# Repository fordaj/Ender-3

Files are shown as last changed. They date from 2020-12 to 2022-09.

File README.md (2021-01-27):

# Ender-3
I run a small print farm for my business, fordworks3D, LLC. It is currently made up of 4 Ender 3 Pros, and this is where you can find my project upgrades, Octoprint network setup, Marlin configurations, and more.

<p align="center">
    <a href="https://www.etsy.com/shop/fordworks3D">fordworks3D Logo</a>
</p>
<p align="center">
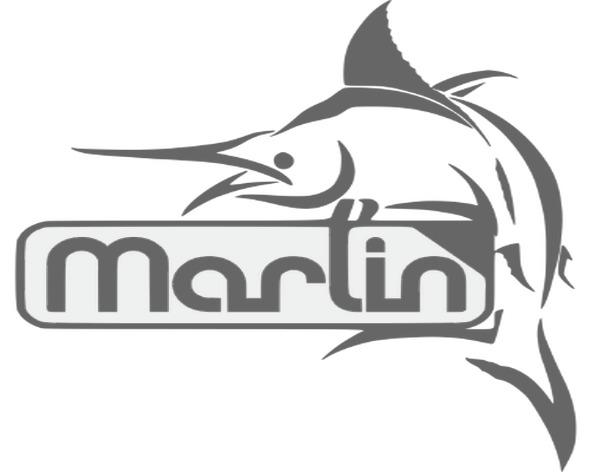
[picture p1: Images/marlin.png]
Marlin Logo
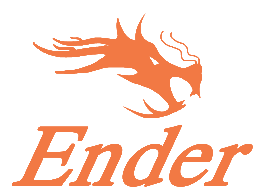
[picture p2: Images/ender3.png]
Ender 3 Logo
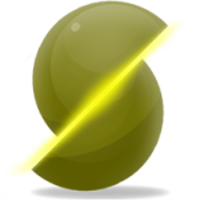
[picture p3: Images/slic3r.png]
Slic3r Logo
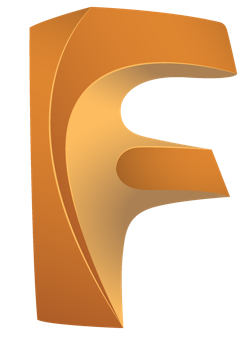
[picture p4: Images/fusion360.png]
Fusion 360 Logo
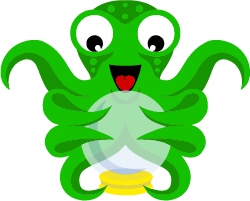
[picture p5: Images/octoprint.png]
Octoprint Logo
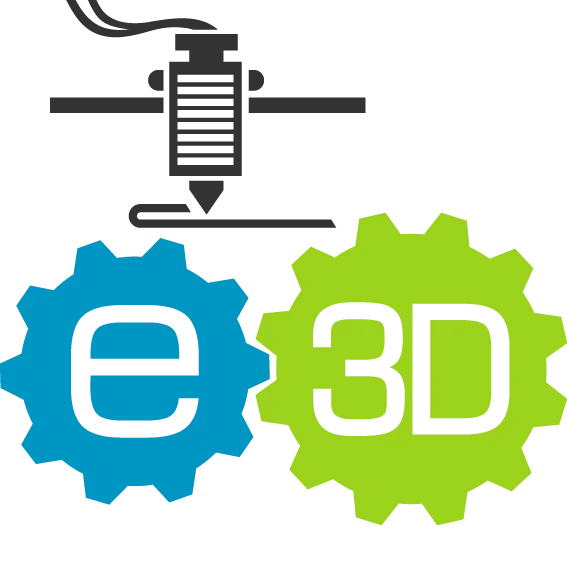
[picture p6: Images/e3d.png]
E3D Logo
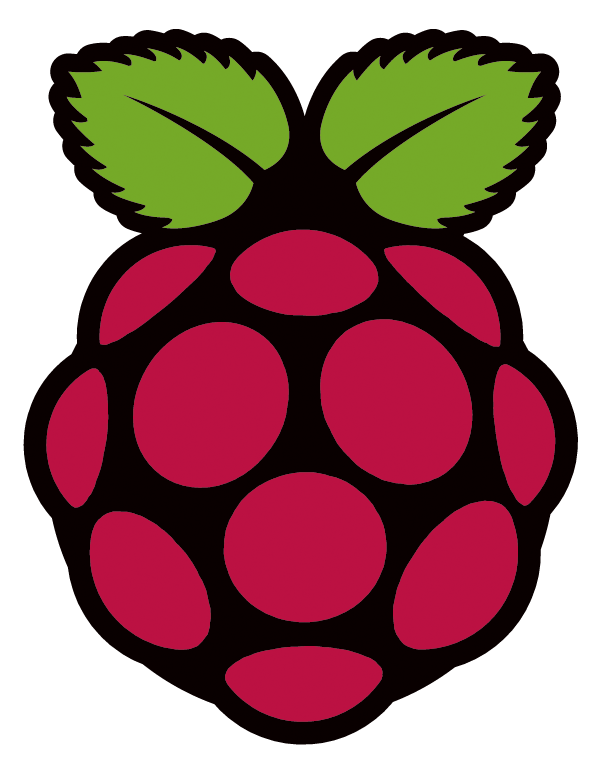
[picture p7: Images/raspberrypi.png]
Raspberry Pi Logo
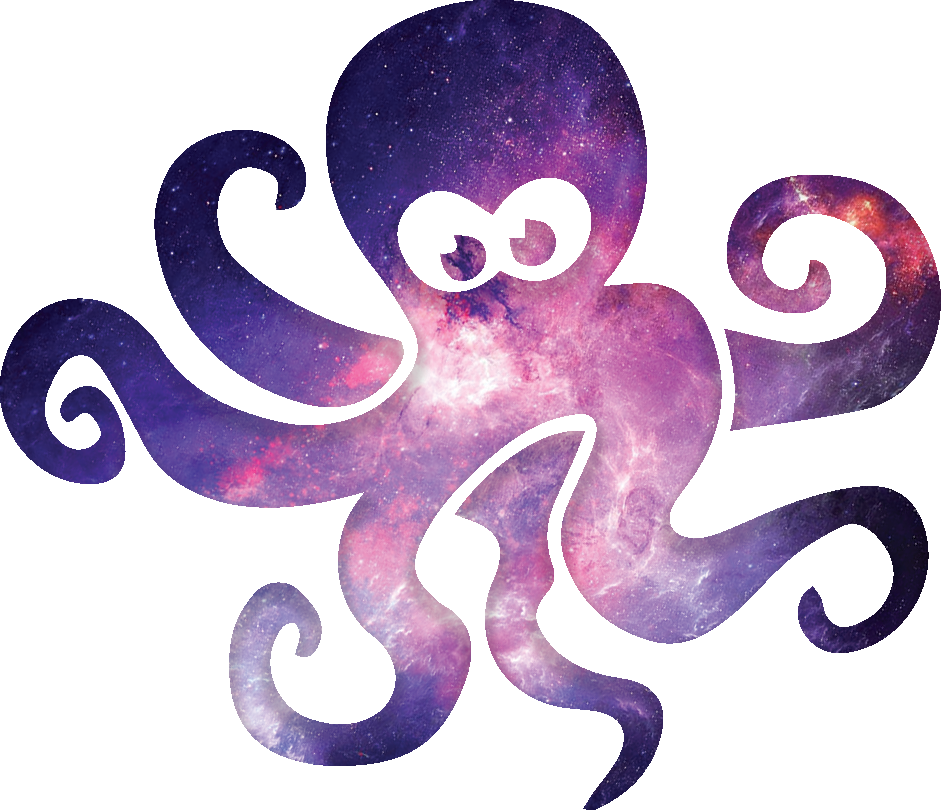
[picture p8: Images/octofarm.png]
Octofarm Logo
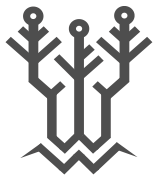
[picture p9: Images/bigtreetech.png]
BIGTREETECH Logo
             
</p>

## Parts List
These are the things I buy when I want to add another printer to the line. Things not included are JST connectors, solder, wire, filament, labels, and other supplies. This list is ordered by priority of what I personally feel are the most to least essential upgrades to your Ender 3. In total, each printer costs ~$700.
| Type | Item | Price |
|--|--|--|
| 3D Printer | [Creality Ender 3 Pro](https://www.creality3dofficial.com/products/creality-ender-3-pro-3d-printer) | $249 |
| Control Board | [BIGTREETECH SKR Mini E3 V2.0](https://www.biqu.equipment/products/bigtreetech-skr-mini-e3-v2-0-32-bit-control-board-integrated-tmc2209-uart-for-ender-3) | $35 |
| Build Plate | [235mm x 235mm x 3mm Borosilicate Glass Bed](https://www.amazon.com/s?k=235mm+borosilicate+glass+bed) | $20 |
| Extruder | [E3D Hemera](https://e3d-online.com/collections/hotends/products/e3d-hemera-direct-kit-1-75mm) | $110 |
| Leveling Probe | [Differential IR Height Sensing Probe](https://www.amazon.com/gp/product/B07RKTQ53F/ref=ppx_yo_dt_b_asin_title_o00_s00?ie=UTF8&psc=1) | $16 |
| Cooling Fans | [24V Brushless High Speed Radial Fans](https://www.amazon.com/WINSINN-Bearing-50x50x15mm-Extruder-Makerbot/dp/B07DB7DLMM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) | $10 |
| Hotend | [E3D Supervolcano Kit with Extra Nozzles](https://e3d-online.com/collections/hotends/products/supervolcano-upgrade-kit) | $117 |
| Octoprint Host | [Raspberry Pi 4 B, 4GB RAM with Heatsinks and Power Supply](https://vilros.com/collections/raspberry-pi-4/products/raspberry-pi-4-4gb-ram) | $78 |
| Mini USB | [USB Type A to Mini B Cable, 3ft](https://www.amazon.com/s?k=Mini+usb+cable&ref=nb_sb_noss_2) | $10 |
| Camera | [Raspberry Pi Camera, 1080p, 5MP](https://www.amazon.com/s?k=raspberry+pi+cam&ref=nb_sb_noss) | $10 |
| Smart Outlet | [Wemo Mini Smart Outlet](https://www.bestbuy.com/site/wemo-mini-wifi-smart-plug-white/5711458.p?skuId=5711458&ref=212&loc=1) | $20 |
| Table | [(x2) Ikea Lack Endtable](https://www.ikea.com/us/en/p/lack-side-table-black-20011408/) | $20 |

## Software Used
Relevant files and setup instructions are linked accordingly.
| Category | Name | Description |
|--|--|--|
| Firmware | [Marlin](https://marlinfw.org) | Open source firmware for configuring your 3D printer/CNC/Laser. My files can be found here (LINK) |
| STL Slicer | [Slic3r](https://slic3r.org) | Open source STL slicer. Profiles found here (LINK) |
| CAD | [Fusion 360](https://www.autodesk.com/products/fusion-360/overview) | Autodesk's cross-platform, free for non-commercial use CAD software (See [startup edition](https://www.autodesk.com/products/fusion-360/startups) for small businesses) |
| Printer Controller | [Octoprint](https://octoprint.org) | An open source web interface for 3D printer monitoring and control. |
| Farm Viewer | [Octofarm](https://octofarm.net) | Open source web server/client for managing several Octoprint instances. |

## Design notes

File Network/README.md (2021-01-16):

# Octoprint
This README details the setup and configuration of Octoprint on a Raspberry Pi 3 and up.

# Raspberry Pi Setup

### Preparation
- Download and install [Etcher](https://www.balena.io/etcher/)
- Download [Octoprint OS image](https://octoprint.org/download/)
- Micro SD card with sufficient memory plugged into PC/Mac

### Setup remote login
1. Write Octoprint OS to micro SD card using Etcher
2. Add your network information to [octopi-wpa-supplicant.txt](octopi-wpa-supplicant.txt) and copy edited file into the root folder on the new drive "boot"
3. Insert micro SD card into pi, plug in and power on
4. Get IP address from router
5. In client terminal, add a new IP alias "printer##" to the list
```
sudo nano /etc/hosts
```
6. In client terminal, run "ssh pi@printer##" and login with password "raspberry"

### Password, SSH keys, Hostnames
1. Change password
```
passwd
```
2. Change the hostname from "octoprint" to printer##
```
sudo nano /etc/hostname
sudo nano /etc/hosts
```
3. Generate key pair. Save in a file you'll know the name of (ex. /home/pi/.ssh/myLaptop), and if you prefer, enter a passphrase
```
ssh-keygen
```
4. Logout, and then copy the host key to the client
```
logout
...
ssh-copy-id pi@printer##
```
5. Reboot the pi
```
ssh pi@printer##
...
sudo reboot
```

# Octoprint Setup
1. Follow the setup prompt, with a username and password login
2. Keep Access Control Enabled
3. Disable Anonymous Usage Tracking
4. Test host & port, and Enable Connectivity Check
5. Enable Plugin Blacklist Processing
6. Name the printer and model
7. Width and Depth: 235mm, Height: 250mm
8. Nozzle Diameter: 1.2mm
3. In the dashboard, check the "Auto-connect on server startup" box
### Appearance
1. Change "Title" to the name of the printer
2. Change the color however you'd like

# Plugins
Settings > Plugin Manager > Get more... > Search for specific plugins

### Continuous Print
1. Search "Continuous Print" and install
2. Reboot

### Cost estimator
1. Search "Cost estimator" and install
2. Reboot
3. Configure cost based on volumetric flow rate **NEEDS UPDATED**

### Firmware Updater
1. Search "Firmware Updater" and install
2. Reboot
3. Follow the settings in the [repository documentation's](https://github.com/OctoPrint/OctoPrint-FirmwareUpdater#lpc1768-boards) LPC1768 section
- Run the following command (if not already shown in the repository)
```
sudo chmod 777 /media/usb0
```
4. Settings > Firmware Updater > Wrench Icon:
- Flash Method: LPC1768
- Path to firmware folder: 
```
/media/usb/
```
- Clicking "Test" should show "Path is valid". If "Path is not writeable" is shown, repeat steps 3 and 4.
- Check "Enable Navbar Icon" box
5. Reboot before using

### GitFiles
1. Search "OctoPrint-GitFiles" and install
2. Reboot
3. Set up SSH for cloning into Github repository
```
ssh pi@printer##
```
```
ssh-keygen
<enter for id_rsa>
<enter passphrase if desired>
cat ~/.ssh/id_rsa.pub
```
- Copy everything except "pi@printer##"
4. Add the SSH key to your github account
- Github.com > Account icon > Settings > SSH and GPG Keys > New SSH key
- Name: "printer##"
- Key: Paste the key copied from step 3
5. Octoprint > Settings > GitFiles
- Paste the SSH url into the URL field
- Rename "gitfiles" to "Products"

### Navbar Temperature Plugin
1. Search "Navbar Temp" and click "Install"
2. Reboot before using
3. Once complete, go to "Settings > Navbar Temperature Plugin > SoC name to display" and change it to "Pi"

### OctoPod Notifications
1. Search "OctoPod" and install
2. Reboot
3. Display progress: 100%
4. Set all other degrees/times to 0

### OctoPrint-PrintTimeGenius
1. Search "OctoPrint-PrintTimeGenius" and install
- Note: Files preprocessed by OctoPrint-PrintTimeGenius will be marked with a yellow star
2. Reboot before using

### Themeify
1. Search "Themeify" and install
2. Reboot
3. Choose a theme (discoranged!) in Settings > Themeify > Theme

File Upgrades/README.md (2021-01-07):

# Cable Guides
[Thing](https://www.thingiverse.com/thing:2920060) by [johnniewhiskey](https://www.thingiverse.com/johnniewhiskey/designs). Not yet printed

# Direct Drive
[Thing](https://www.thingiverse.com/thing:3589452/files) by [Madau3D](https://www.thingiverse.com/madau3d/designs). A simple bracket fixing the extruder a short distance above the hotend. One consideration is that the extruder stepper motor wire will be too short without reducing the length of the hotend cables. This is not required with a Hemera installed.
### Considerations
Your nozzle choice, as well as printer settings, may change the length of PTFE tubing required for assembly. I have found that 10cm of PTFE tubing snugs the extruder stepper against the upper limits of the bracket with the Capricorn PTFE attachments.

# Fan Shroud
<p align="center">
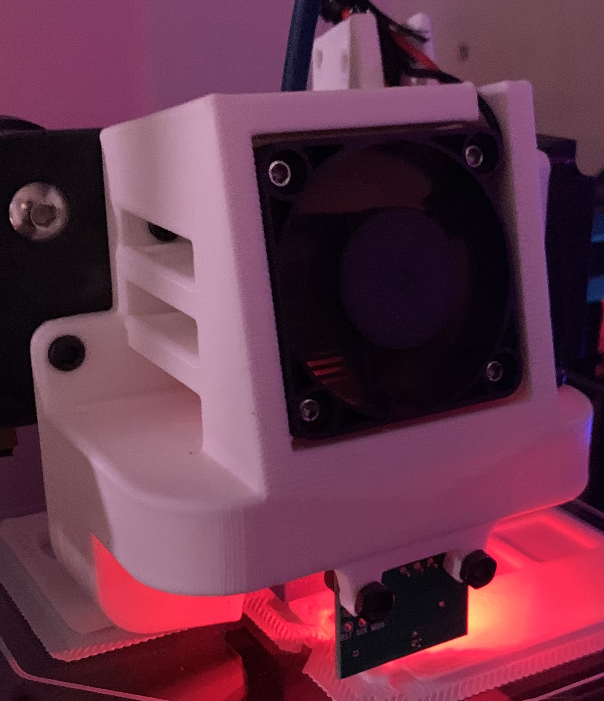
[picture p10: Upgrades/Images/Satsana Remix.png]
Satsana Remix
    
</p>

[Thing](https://www.thingiverse.com/thing:4369859) by [eric-anastas](https://www.thingiverse.com/eric-anastas/designs). Redesigned by me to fit the E3D Volcano heater block, and to mount the Duet IR probe clone.
### Considerations
Drilled out holes in part cooling fan to use M3 socket head bolts instead of M2. I find that M2 bolts, as well as button head M3 bolts will strip and wear down the allen wrenches. M3 socket head bolts use a larger M4 sized Allen wrench, allowing for plenty of torquing before failure.

# IKEA LACK Table Enclosure
## Filament Guide
[Thing](https://www.thingiverse.com/thing:2580051/makes) by [JayMake](https://www.thingiverse.com/jaymake/designs). Requires bolts, nuts, and ball bearings.

## Leg Brackets
[Thing](https://www.thingiverse.com/thing:2119747/files) by [Pr0teinAddict](https://www.thingiverse.com/pr0teinaddict/designs). Requires drywall screws around 1" long. Intended to reduce printer wobbling caused by lower table legs. Not yet printed.

## Spool Holder
[Thing](https://www.thingiverse.com/thing:2864118/files) by [cisardom](https://www.thingiverse.com/cisardom/designs). All-plastic spool roller for mounting on the top LACK table. Drywall screws recommended.

# LED Strip Mounting Bar
[Thing](https://www.thingiverse.com/thing:3272248/files) by [LilTrublMakr](https://www.thingiverse.com/LilTrublMakr). Not yet printed

# Power Supply Fan Silencer
[Thing](https://www.thingiverse.com/thing:3328495) by [RohaniSousBois](https://www.thingiverse.com/RohaniSousBois). Not yet printed or downloaded.

# Raspberry Pi 4 Mount
[Thing](https://www.thingiverse.com/thing:4586351) by [eoyilmaz](https://www.thingiverse.com/thing:4586351). Not yet printed or downloaded.

# V-Slot Track Covers
[Thing](https://www.thingiverse.com/thing:3379068/files) by [ximes](https://www.thingiverse.com/ximes). Not yet printed or downloaded.

# X Belt Tensioner
[Thing](https://www.thingiverse.com/thing:3319649) by [Misterguru](https://www.thingiverse.com/misterguru/designs).
Not yet printed

# Y Belt Tensioner
[Thing](https://www.thingiverse.com/thing:3268192) by [Misterguru](https://www.thingiverse.com/misterguru/designs).
Not yet printed

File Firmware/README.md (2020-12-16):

# Marlin Firmware
Last built version 2.0.7.0.2 on 12-13-20.

# Configurations for multiple printers
It is all too easy to let your printers fall into different states. Of my 4 Ender 3 Pros, 3 have BL Touches and SKR Mini E3 V1.2s, one has an E3D Supervolcano, the others have volcano clones, and the list goes on. Rather than make global changes every time I want to try out a potential upgrade, I find it easier to use conditional preprocessor directive definitions that can be switched simply by altering one number. For printer 4, my [Configuration.h](Marlin/Configuration.h) has the following line of code at the top:
```cpp
#define PRINTER_NUMBER 4
```
This parameter can be referenced conditionally by [Configuration.h](Marlin/Configuration.h), [Configuration_adv.h](Marlin/Configuration_adv.h), [__Statusscreen.h](Marlin/__Statusscreen.h), and [__Bootscreen.h](Marlin/__Bootscreen.h). I started with the Creality > Ender 3 Pro > SKR 1.2 configuration files in Marlin's [configuration repository](https://github.com/MarlinFirmware/Configurations).

# __Bootscreen.h
1. Generate a 128px x 64px black-and-white (not grayscale) [image](https://docs.google.com/drawings/d/1esvaDp8sekXSNG2BmdKc_YW7rbkxW2ErX6xhDDlnSYM/edit?usp=sharing)
2. Convert .png to .bmp with Marlin's [online bitmap converter](https://marlinfw.org/tools/u8glib/converter.html), with the "Boot" button selected.
3. Copy the code into [__Bootscreen.h](Marlin/__Bootscreen.h).

# __Statusscreen.h
1. Generate a 25px x 25px black-and-white (not grayscale) [image](https://docs.google.com/drawings/d/14gHQIaz-qxfSjFEl2ztzSXw9ercS4QekcHenZl6bkp0/edit?usp=sharing)
2. Convert .png to .bmp with Marlin's [online bitmap converter](https://marlinfw.org/tools/u8glib/converter.html). Be sure to select "Status", "Bed", "Fan", and set Nozzles to 1.
3. Copy the code into [__Statusscreen.h](Marlin/__Statusscreen.h), and edit the if statements as needed.

# Configuration.h
The changes I made to the SKR Mini E3 V1.2 [Configuration.h](Marlin/Configuration.h) file from Marlin's configuration repository are listed below.
## Setup
```cpp
#define PRINTER_NUMBER 4

#define STRING_CONFIG_H_AUTHOR "(Andrew Ford, fordworks3D LLC)"

//#define SHOW_BOOTSCREEN

#define SHOW_CUSTOM_BOOTSCREEN

#define CUSTOM_STATUS_SCREEN_IMAGE

#if PRINTER_NUMBER == 1:
  #define CUSTOM_MACHINE_NAME "printer01"
#elif PRINTER_NUMBER == 2:
  #define CUSTOM_MACHINE_NAME "printer02"
#elif PRINTER_NUMBER == 3:
  #define CUSTOM_MACHINE_NAME "printer03"
#elif PRINTER_NUMBER == 4:
  #define CUSTOM_MACHINE_NAME "printer04"
#else:
  #define CUSTOM_MACHINE_NAME "Ender-3 Pro"
#endif
```

## Thermal Settings
```cpp
#if PRINTER_NUMBER == 1:
  #define TEMP_SENSOR_0 1   // Stock Thermistor
#elif PRINTER_NUMBER == 2:
  #define TEMP_SENSOR_0 1   // Stock Thermistor
#elif PRINTER_NUMBER == 3:
  #define TEMP_SENSOR_0 1   // Stock Thermistor
#elif PRINTER_NUMBER == 4:
  #define TEMP_SENSOR_0 5   // E3D Thermistor
#else:
  #define TEMP_SENSOR_0 1   // Stock Thermistor
#endif
```

## Z Probe Options
```cpp
#if PRINTER_NUMBER == 2:
  #define BLTOUCH           // BLTouch Clone
#elif PRINTER_NUMBER == 3:
  #define BLTOUCH           // BLTouch Clone
#elif PRINTER_NUMBER == 4:
  #define BLTOUCH           // BLTouch Clone
#endif
```

## Bed Leveling
```cpp
#if PRINTER_NUMBER == 1:
  #define MESH_BED_LEVELING
#elif PRINTER_NUMBER == 2:
  #define AUTO_BED_LEVELING_3POINT
#elif PRINTER_NUMBER == 3:
  #define AUTO_BED_LEVELING_3POINT
#elif PRINTER_NUMBER == 4:
  #define AUTO_BED_LEVELING_3POINT
#else:
  //#define AUTO_BED_LEVELING_3POINT
  //#define AUTO_BED_LEVELING_LINEAR
  //#define AUTO_BED_LEVELING_BILINEAR
  //#define AUTO_BED_LEVELING_UBL
  #define MESH_BED_LEVELING
#endif

// Use "Z Safe Homing" to avoid homing with a Z probe outside the bed area.
#if PRINTER_NUMBER == 2:
  #define Z_SAFE_HOMING
#elif PRINTER_NUMBER == 3:
  #define Z_SAFE_HOMING
#elif PRINTER_NUMBER == 4:
  #define Z_SAFE_HOMING
#endif
```

## Additional Features
```cpp
// Preheat Constants
#define PREHEAT_1_LABEL       "PLA"
#define PREHEAT_1_TEMP_HOTEND 200
#define PREHEAT_1_TEMP_BED     60
#define PREHEAT_1_FAN_SPEED     0 // Value from 0 to 255

#define PREHEAT_2_LABEL       "ABS"
#define PREHEAT_2_TEMP_HOTEND 240
#define PREHEAT_2_TEMP_BED    110
#define PREHEAT_2_FAN_SPEED     0 // Value from 0 to 255

// Babystepping
#define BABYSTEP_MILLIMETER_UNITS       // Specify BABYSTEP_MULTIPLICATOR_(XY|Z) in mm instead of micro-steps
#define BABYSTEP_MULTIPLICATOR_Z  0.001       // (steps or mm) Steps or millimeter distance for each Z babystep
#define BABYSTEP_MULTIPLICATOR_XY 0.001 

#define BABYSTEP_ZPROBE_OFFSET          // Combine M851 Z and Babystepping

//Linear Advance 
//#define LIN_ADVANCE

```

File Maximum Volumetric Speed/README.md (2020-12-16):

# Maximum Volumetric Speed (MVS)
The name of the game when running a print farm is to achieve the **highest part throughput** in the **most cost effective manner** possible. The last thing I want to do is drop another $400+ on a new printer, when it might be an option to speed up the printers that I've already got. Therefore, working within my personal constraints, my goal is to raise my **Maximum Volumetric Speed** as high as possible. Some slicers have a setting for MVS, which will ensure that your print speeds stay below the mm^3/s value that you specify. Anything that the filament touches on its way to the build plate affects MVS, so let's look at things step by step to reduce MVS bottlenecks.

# Filament
The first consideration is filament. Most are documented in a technical datasheet containing their **Melt Flow Index (MFI)**, which is inversely proportional to viscosity. Higher MFI = higher MVS. MFI is obtained using a standardized procedure, requiring that a 3.2kg plunger push a material at a steady temperature through a small hole. Often, more expensive filaments hold a higher MFI, but this is not always the case. Take eSun's breakdown of their different filament types:
| Material | MFI (g/10min) | Temperature (ºC) | Density (g/cm^3) |
|--|--|--|--|
| PLA | 5 | 190 | 1.25 |
| ABS | 12 | 220 | 1.04 |
| PETG | 6.6 | 230 | 1.23 |
| Wood | 17 | 190 | 0.7 |
Some materials will flow much slower than others, such as PETG. Since cost is a priority for me, I chose to work exclusively with PLA, since it can often be found spooled for less than $20/kg.

| Material | Brand | MFI (g/10min @ 190ºC) | MFI (g/10min @ 210ºC) |  Spooled Cost ($/kg) | Pelletized Cost ($/kg) |
|--|--|--|--|--|--|
| PLA 4043D | NatureWorks | - | 6 | - | - |
| PLA LX175 | Luminy | 3 | 8 | - | $7.50 |
| PLA+ | eSun | 4 | - | $18.99 | - |
| PLA | eSun | 5 | - | $16.99 | - |

The filament's theoretical MVS can be calculated by multiplying the MFI and MVS:
<p align="center">MVS=V/t=m/(d*t)=MFI*d</p>
<p align="center">esunPLAMVS</p>
Given that the test includes a 3.2kg weight, the force applied is ~32N.

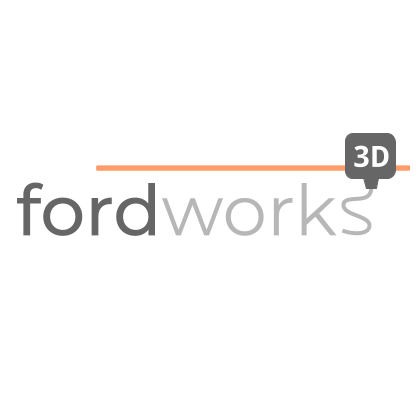
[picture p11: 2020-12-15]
Images/fordworks3D2.png

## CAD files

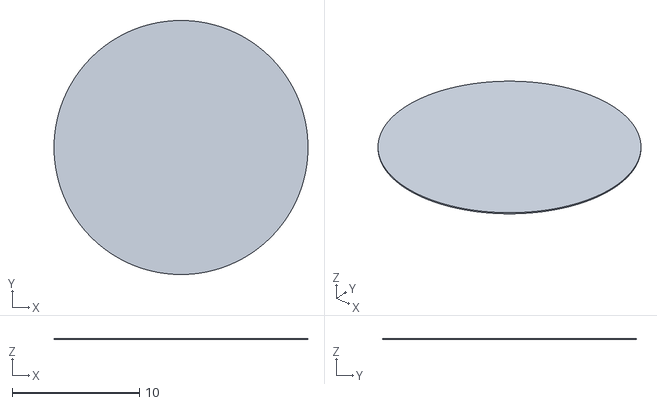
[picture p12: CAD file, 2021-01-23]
Calibration/Single_Layer_Disc.stl
20.0 x 20.0 x 0.1

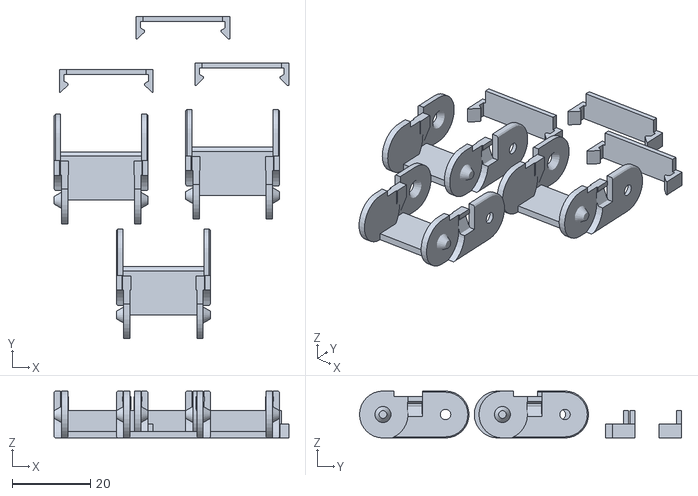
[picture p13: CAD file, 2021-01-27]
Upgrades/Cable Guides/3CableLinks.stl
59.9 x 82.3 x 12.0

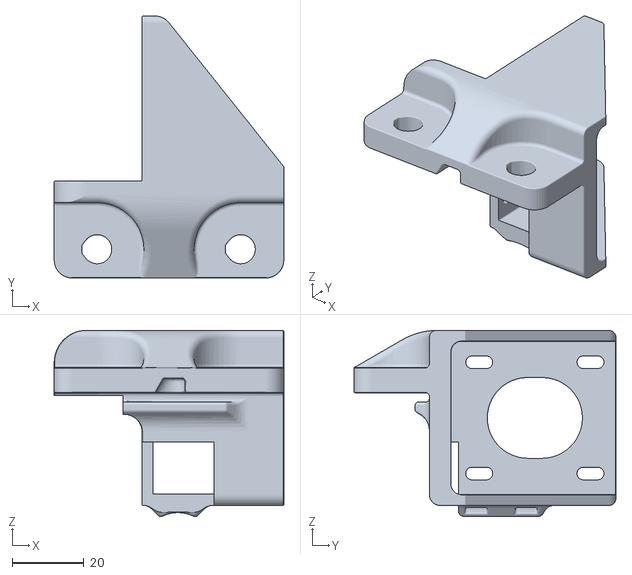
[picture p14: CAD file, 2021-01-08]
Upgrades/Direct Drive/directDriveBracket.stl
64.0 x 73.0 x 51.9

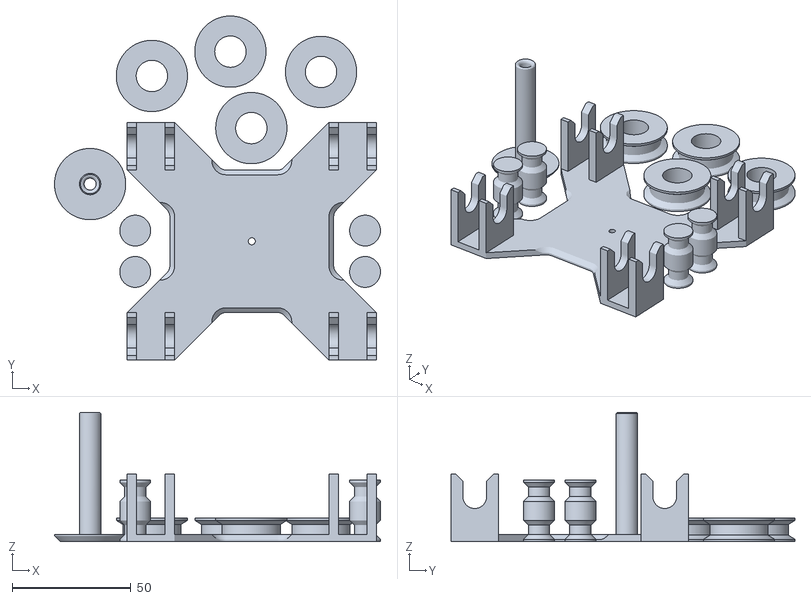
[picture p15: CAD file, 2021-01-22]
Upgrades/Enclosure/Prusa_Enclosure_Spool_Holder.stl
137.3 x 144.9 x 54.5

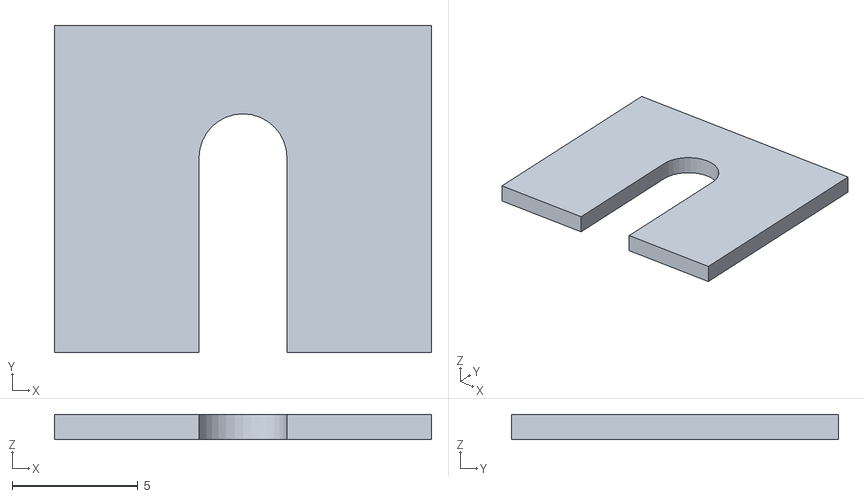
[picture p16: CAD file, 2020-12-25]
Upgrades/Feeder Spring Shims/Shim_1mm.stl
15.0 x 13.0 x 1.00

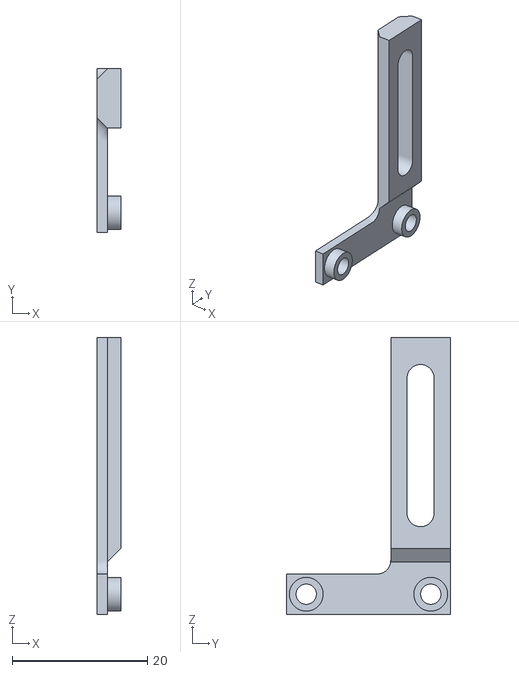
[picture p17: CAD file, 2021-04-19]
Upgrades/Hemera/probe_mount.stl
3.61 x 24.2 x 41.0

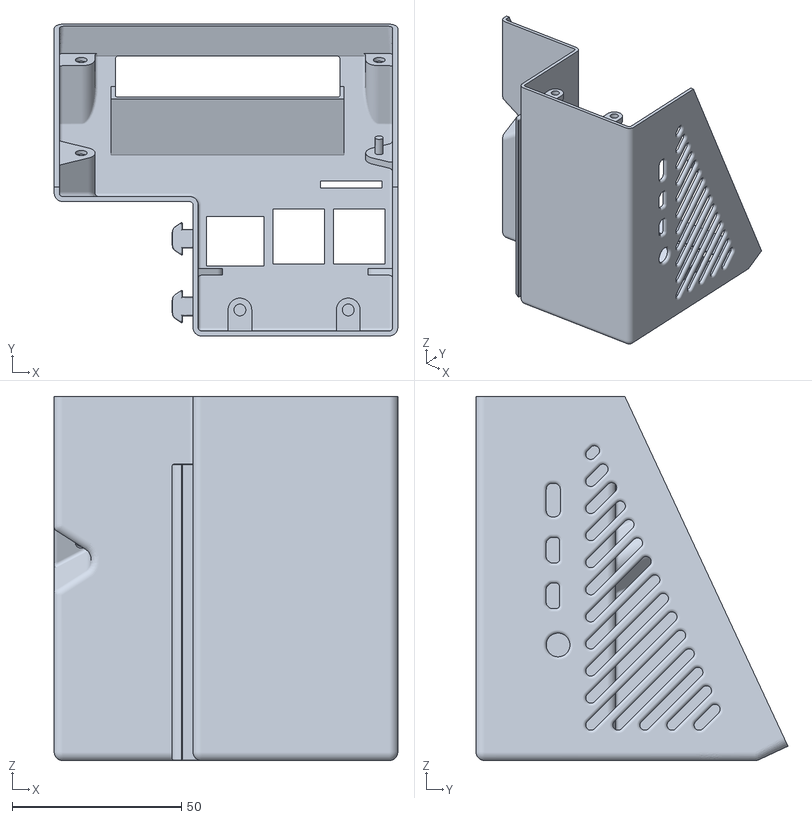
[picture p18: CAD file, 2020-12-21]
Upgrades/Raspberry Pi 4 Mount/Raspberry_Pi_2_Case_For_Creality_Ender_3_Pro_v054.stl
101.5 x 92.2 x 107.5

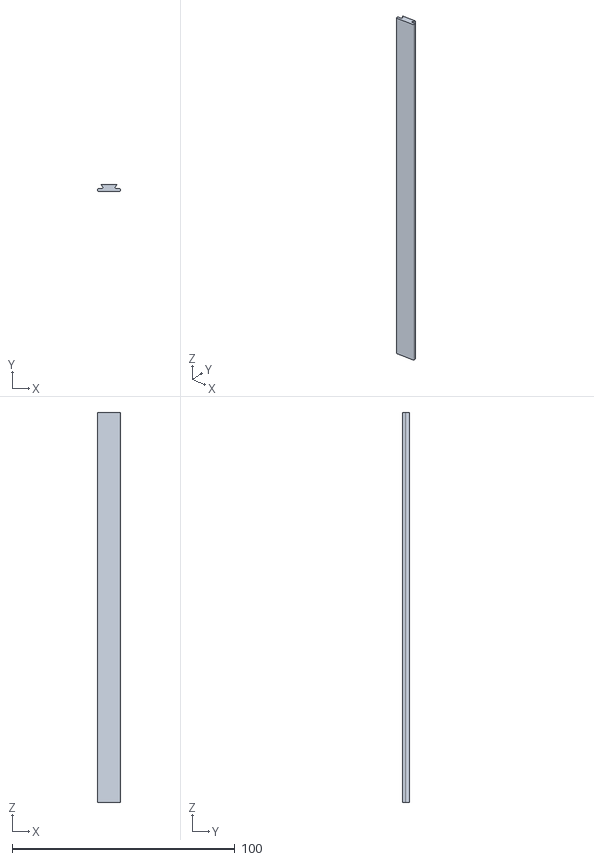
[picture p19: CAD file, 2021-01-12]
Upgrades/V-Slot Covers/slot_cover_175mm.stl
10.2 x 3.23 x 175.0

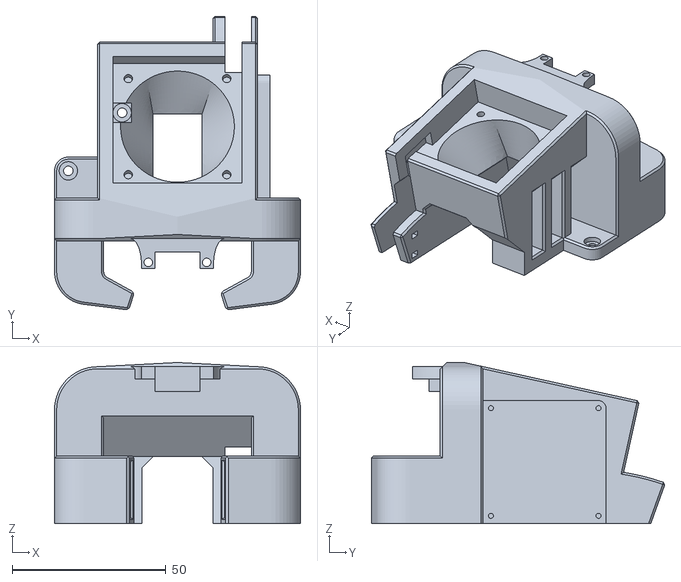
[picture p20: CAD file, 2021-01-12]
Upgrades/Volcano Duct/volcanoFanDuct.stl
80.0 x 95.4 x 52.4

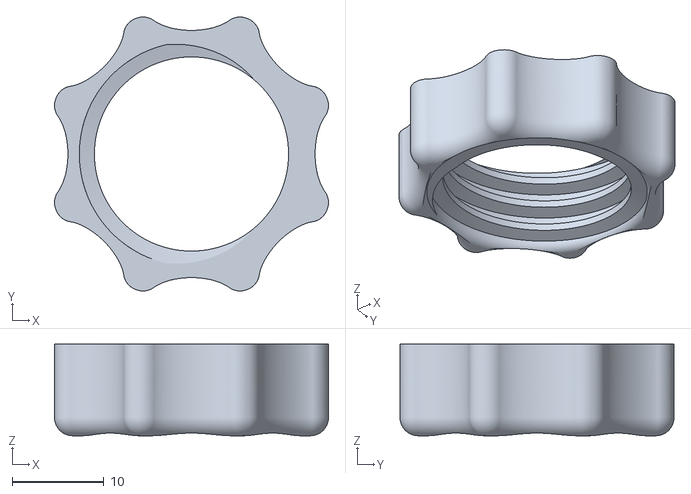
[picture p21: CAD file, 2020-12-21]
Upgrades/X Belt Tensioner/knob.stl
29.9 x 29.9 x 10.0

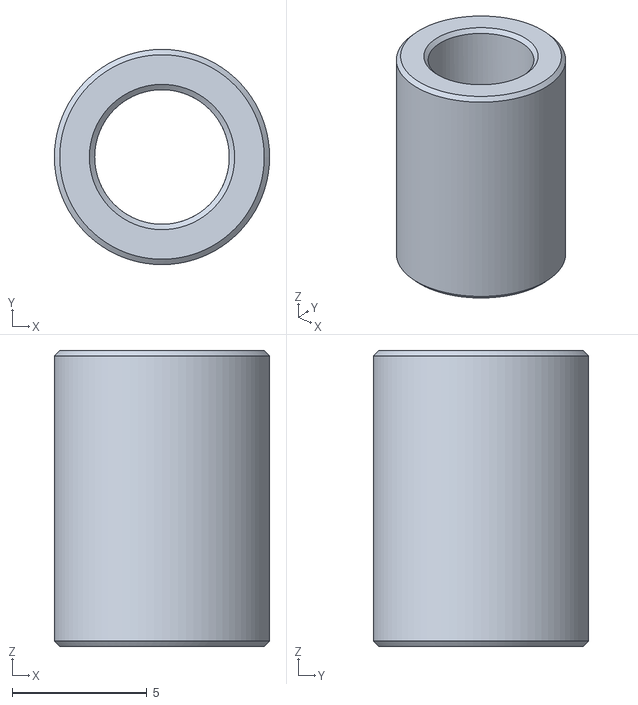
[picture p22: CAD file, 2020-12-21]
Upgrades/Y Belt Tensioner/bushing.stl
8.00 x 8.00 x 11.0

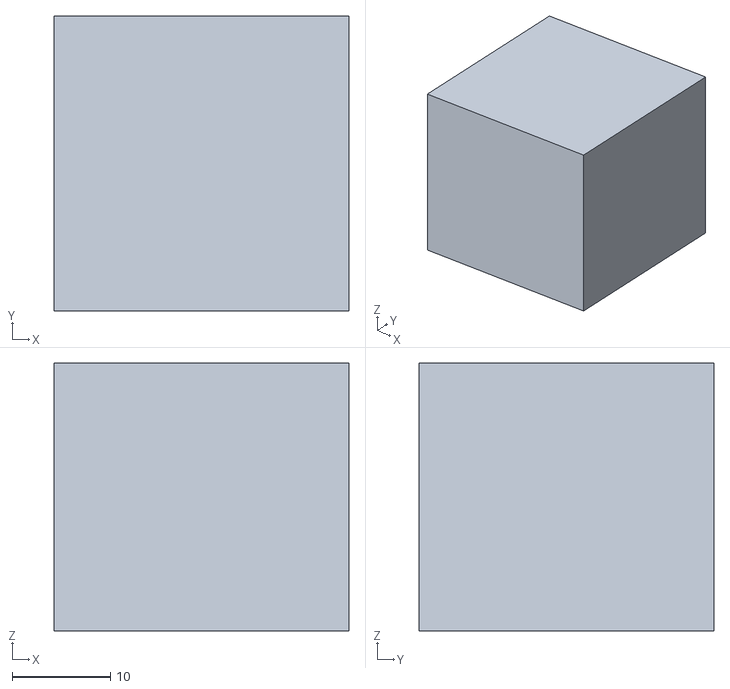
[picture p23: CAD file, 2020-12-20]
Calibration/cube.stl
30.0 x 30.0 x 27.2

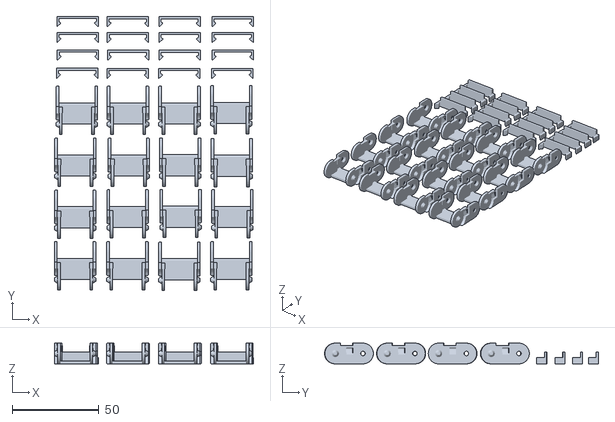
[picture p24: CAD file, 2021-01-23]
Upgrades/Cable Guides/16CableLinks.stl
115.1 x 158.3 x 12.0

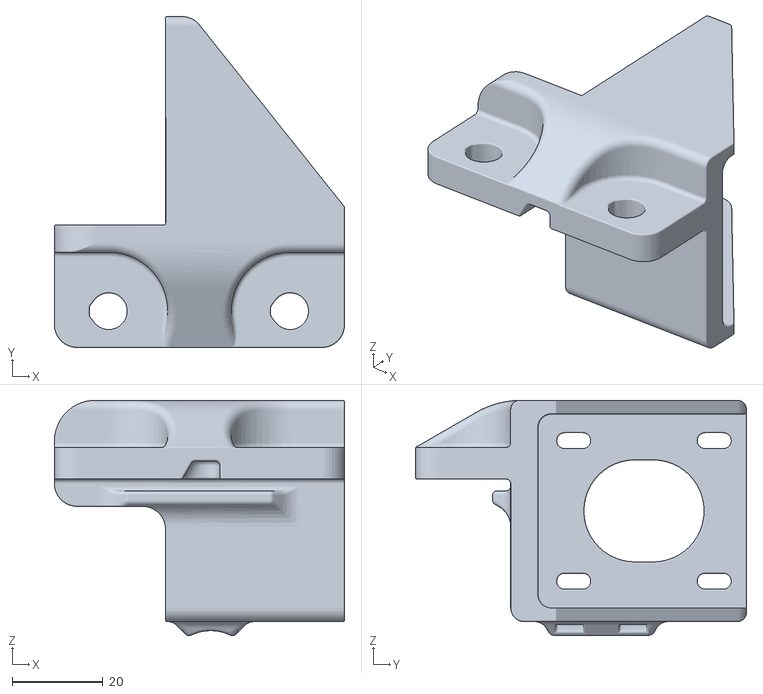
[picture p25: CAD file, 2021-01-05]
Upgrades/Direct Drive/direct_drive_extruder_bracket_v1.3.STL
64.0 x 73.0 x 51.9

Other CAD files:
Upgrades/Enclosure/legExtension.stl
Upgrades/Feeder Spring Shims/Shim_2mm.stl
Upgrades/Hemera/Ender3-Hemera_V4.stl
Upgrades/V-Slot Covers/slot_cover_105mm.stl
Upgrades/Cable Guides/cableChain_40MountSide_v2.stl
Upgrades/Cable Guides/cableChain_40MountTop_v2.stl
Upgrades/Cable Guides/cableChain_Xend.stl
Upgrades/Cable Guides/cableChain_XendCover.stl
Upgrades/Cable Guides/cableChain_bedCornerCover_v2.stl
Upgrades/Cable Guides/cableChain_bedCorner_v2.stl
Upgrades/Cable Guides/cableChain_linkCover_v2.stl
Upgrades/Cable Guides/cableChain_link_v3.stl
Upgrades/Enclosure/IKEA-LACK-BRACKET-DRYWALL-SCREWS.stl
Upgrades/Enclosure/lackLegExtender.stl
Upgrades/Hemera/cooling_duct.stl
Upgrades/V-Slot Covers/slot_cover_143mm_original.stl
Upgrades/X Belt Tensioner/body.stl
Upgrades/X Belt Tensioner/pulleyCarriage.stl
Upgrades/Y Belt Tensioner/body.stl
Upgrades/Y Belt Tensioner/nut.stl
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

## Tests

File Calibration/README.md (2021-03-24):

# Calibration

## PID Tuning
Any changes affecting the thermals of the printer should be followed with appropriate PID tuning. Installing a new glass bed, new heat break, fans, nozzle material, etc. all impact the printer's heating rates.
### Hotend
PID auto-tuning for the hotend can be run with M303 from host software (pronterface, octoprint, etc). For accurate results, run 15 cycles with the average of all temperatures you expect to print at for accurate results:
```gcode
M303 E0 S260 C15   ; Auto-tune PID values for hotend with 10 cycles 0C to 260C
```
After completion, be sure to copy the new values into Configuration.h. The values can be saved to the printer without rebuilding firmware:
```gcode
M301 P24.76 I1.91 D80.16    ; Write new PID values to EEPROM
M500                        ; Store settings
M501                        ; Load settings
```
Common issues:
1. **No silicone sock on the heater block**: Since the Ender 3 fan blows onto the entire hotend, it prevents the heater block from reaching temperature.
2. **Faulty thermistor/connection/wrong thermistor number in Marlin**: The temperature varies wildly.
3. **Faulty heater cartridge/connection**: Unable to heat up/heats intermittently.
4. **PID settings aren't enabled in Marlin**: Will show up as "Bad extruder number!" when running commands.

### Bed
PID auto-tuning for the bed can be run with an M304:
```gcode
M303 E-1 S60 C15   ; Auto-tune PID values for bed with 5 cycles 0C to 60C
```
Note: If this line of code produces an error "Bad extruder number!", it is likely that PID Bed Temp is not enabled in Marlin.
After completion, be sure to copy the new values into Configuration.h. The values can be saved to the printer without rebuilding firmware:
```gcode
M304 P99.85 I11.14 D596.73  ; Write new PID values to EEPROM
M500                        ; Store settings
M501                        ; Load settings
```

## E-steps
1. Heat the nozzle to the temperature you'll be printing with
2. Put the printer in relative position, and print out the old e-step value
```gcode
G91 ; Relative positioning
M92 ; The "E" parameter is the old e-step value
```
3. Mark the filament with a marker as close to the extruder as possible
4. Make another mark on the incoming filament 120mm away from the first mark
5. Turn the extruder knob to push filament through the hotend until your first mark lines up with the beginning of the extruder
6. Extrude 100mm of filament
```gcode
G1 E100 F50    ; Extrude 100mm of filament at 50mm/s
```
7. New_ESteps = Old_ESteps * 100 / (120 - length_remaining) (Teaching Teach offers an [e-step calculator](https://teachingtechyt.github.io/calibration.html#esteps))
8. Write New_ESteps to the printer
```gcode
M92 E188 ; Write e-steps to printer
M500     ; Store settings
M501     ; Load settings
```
8. Repeat steps 3-7 until the length_remaining is 20mm

## Linear Advance
Print [linearAdvance](linearAdvance.gcode) from Marlin's linear advance [gcode generator](https://marlinfw.org/tools/lin_advance/k-factor.html). The value next to the line which looks best can be saved in [Configuration_adv.h](https://github.com/fordaj/Ender-3/blob/main/Firmware/Marlin/Configuration_adv.h)
```cpp
#define LIN_ADVANCE_K 0.3    // Unit: mm compression per 1mm/s extruder speed
```

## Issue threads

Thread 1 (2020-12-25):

Missing hotend collet clip

fordaj, 2020-12-25:

Closed 2020-12-25.

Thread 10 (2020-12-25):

Board not upgraded

fordaj, 2020-12-25:
### Issue
The printer still has the stock Ender 3 Pro Creality board. This comes along with more difficulty updating firmware, no ABL, programmable memory limitations, etc.
### Solution
Install SKR Mini E3 V2.0

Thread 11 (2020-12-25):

Heating failed on E0

fordaj, 2020-12-25:
### Issue
During heating, error occurs causing the printer to beep and the LCD to request a reboot
### Solutions
- Check thermistor connection, replace thermistor if it is shorted or broken
- Check heater cartridge (Ender 3 Pro has 24V 40W, E3D yellow is 24V 30W and fails heating)

Closed 2021-01-08.

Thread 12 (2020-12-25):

Board fan and part cooling fan wires switched

fordaj, 2020-12-25:
### Issue
The SKR Mini E3 V1.2 has the fan pins visually switched relative to the stock Ender 3 board, resulting in part cooling controlling the motherboard fan, and vice versa
### Solution
Switch the pins in hardware, matching Marlin's defaults

Closed 2021-01-08.

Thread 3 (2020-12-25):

printer02: Feeder spring too compressed

fordaj, 2020-12-25:
Likely a global issue contributing to intermittent under-extrusion

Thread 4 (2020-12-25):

Groove worn into brass feeder drive gear

fordaj, 2020-12-25:
Scope: Global
Cause: Abrasive filament wearing out brass feeder gear
Solution: Replace with [steel drive gear](https://www.amazon.com/gp/product/B01J5ON2Y2/ref=ox_sc_act_title_1?smid=A1LCDIR1SM8KTJ&psc=1)

Closed 2021-04-20.

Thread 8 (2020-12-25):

Fan shroud too low

fordaj, 2020-12-25:
### Issue
[Volcano fan shroud](https://github.com/fordaj/Ender-3/tree/main/Upgrades/Volcano%20Effector) collides with print
### Solution
Lower the height of the part cooling fan ducts by 3mm

fordaj, 2020-12-25:
My mistake - it was screwed on tilted!

Closed 2020-12-25.

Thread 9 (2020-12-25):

Fan shroud IR probe mount improperly dimensioned

fordaj, 2020-12-25:
### Issue
- [Fan shroud](https://github.com/fordaj/Ender-3/tree/main/Upgrades/Volcano%20Effector) probe mounting holes are spaced too closely together and do not alight with probe holes. Probe is also too high above build plate
- No room for female header mount (collides with heater block)
### Solution
- [X] Increase spacing of holes
- [X] Move mount further from heater block
- [x] Lower by 1.5mm (should leave probe ~2mm above nozzle tip, can sense ~4mm distances)

Closed 2021-01-08.

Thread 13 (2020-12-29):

Inconsistent layer widths

fordaj, 2020-12-29:
### Issue
Inconsistent line width, resulting in a staggered vertical edge.
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
### Solutions
- Enclose printer to ensure consistent ambient temperature
- Verify part cooling is present & fan ducts point towards nozzle tip
- Check belt tension
- Check frame rigidity

fordaj, 2021-01-08:
Part cooling fan wire and motherboard fan wires were switched.

Closed 2021-04-20.

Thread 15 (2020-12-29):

No ABL sensor installed

fordaj, 2020-12-29:
### Issue
No Auto-Bed Leveling (ABL) sensor installed

### Solution
Currently using the duet IR probe clone plugged into the Neopixel pin PC7 on the SKR Mini E3 V1.2 board mounted on a remixed Satsana fan shroud

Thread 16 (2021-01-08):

ABL Not Configured

fordaj, 2021-01-08:
### Issue
Auto-Bed Leveling is either not enabled, or not properly configured.
### Solution
1. Ensure that 3-point ABL is enabled in Configuration.h
2. Enable relevant settings
3. Flash to EEPROM

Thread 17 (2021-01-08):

Fan shroud collides with direct drive bracket

fordaj, 2021-01-08:
### Issue
Upper left portion of fan shroud collides with the lip of the direct drive bracket which holds it onto the x-axis hot end carriage.
### Solution
In Fusion, open STL and extrude material away to accommodate for the lip.

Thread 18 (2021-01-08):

No direct drive bracket installed

fordaj, 2021-01-08:
### Issue
No direct drive bracket installed on the printer - still using the Bowden setup and chewing through PTFE.

### Solution
1. Print of the remixed bracket mentioned in the upgrades section
2. Assemble printer with updated parts
3. Lengthen extruder stepper wire

Closed 2021-04-20.

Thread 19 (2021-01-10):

V-slot covers not installed

fordaj, 2021-01-10:
### Issue
Printer v-slot covers not installed, allowing plastic strands dust, etc. to become trapped in slots

### Solution
- 8x 143mm

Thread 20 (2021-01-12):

Firmware Updater not installed + configured

fordaj, 2021-01-12:
### Issue
The OctoPrint plugin "Firmware Updater" is not installed and configured

### Solution
1. Install from OctoPrint's plugin manager
2. Follow the instructions in documentation for [LPC1768 boards](https://github.com/OctoPrint/OctoPrint-FirmwareUpdater#lpc1768-boards)
3. Elevate permissions for /media/usb0 mentioned in [this forum](https://github.com/OctoPrint/OctoPrint-FirmwareUpdater/issues/137#issuecomment-758502761)

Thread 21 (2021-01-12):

Order JST Connectors

fordaj, 2021-01-12:
- [ ] ‎[XHP-2‎](https://www.digikey.com/en/products/detail/XHP-2/455-2266-ND/555485?itemSeq=350235820) Pin Connectors
- [ ] [XHP-3‎](https://www.digikey.com/en/products/detail/XHP-3/455-2219-ND/1651017?itemSeq=350235906) Pin Connectors
- [ ] [‎SXH-002T-P0.6‎](https://www.digikey.com/en/products/detail/SXH-002T-P0.6/455-2261-1-ND/1651059?itemSeq=350235981) Socket Contact Tin Jumpers

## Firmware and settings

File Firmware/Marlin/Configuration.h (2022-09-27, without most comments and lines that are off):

#define PRINTER_NUMBER 1
#pragma once
#if PRINTER_NUMBER == 1
  #define CONFIG_EXAMPLES_DIR "Creality/Ender-3/BigTreeTech SKR Mini E3 2.0"
#else
  #define CONFIG_EXAMPLES_DIR "Creality/Ender-3 Pro/BigTreeTech SKR Mini E3 1.2"
#endif
#define CONFIGURATION_H_VERSION 020007
#define STRING_CONFIG_H_AUTHOR "(Andrew Ford, fordworks3D LLC)" // Who made the changes.
#define SHOW_BOOTSCREEN
#define SHOW_CUSTOM_BOOTSCREEN
#define CUSTOM_STATUS_SCREEN_IMAGE
#define SERIAL_PORT 2
#define SERIAL_PORT_2 -1
#define BAUDRATE 115200
#if PRINTER_NUMBER == 1
    #define MOTHERBOARD BOARD_BTT_SKR_MINI_E3_V2_0
#else
  #ifndef MOTHERBOARD
    #define MOTHERBOARD BOARD_BTT_SKR_MINI_E3_V1_2
  #endif
#endif
#if PRINTER_NUMBER == 1
  #define CUSTOM_MACHINE_NAME "printer01"
#elif PRINTER_NUMBER == 2
  #define CUSTOM_MACHINE_NAME "printer02"
#elif PRINTER_NUMBER == 3
  #define CUSTOM_MACHINE_NAME "printer03"
#elif PRINTER_NUMBER == 4
  #define CUSTOM_MACHINE_NAME "printer04"
#else
  #define CUSTOM_MACHINE_NAME "Ender-3 Pro"
#endif
#define EXTRUDERS 1
#define DEFAULT_NOMINAL_FILAMENT_DIA 1.75
#if PRINTER_NUMBER == 2
  #define TEMP_SENSOR_0 5   // E3D Thermistor
#else
  #define TEMP_SENSOR_0 1   // Default thermistor
#endif
#define TEMP_SENSOR_1 0
#define TEMP_SENSOR_2 0
#define TEMP_SENSOR_3 0
#define TEMP_SENSOR_4 0
#define TEMP_SENSOR_5 0
#define TEMP_SENSOR_6 0
#define TEMP_SENSOR_7 0
#define TEMP_SENSOR_BED 1
#define TEMP_SENSOR_PROBE 0
#define TEMP_SENSOR_CHAMBER 0
#define DUMMY_THERMISTOR_998_VALUE 25
#define DUMMY_THERMISTOR_999_VALUE 100
#define MAX_REDUNDANT_TEMP_SENSOR_DIFF 10
#define TEMP_RESIDENCY_TIME     10  // (seconds) Time to wait for hotend to "settle" in M109
#define TEMP_WINDOW              1  // (°C) Temperature proximity for the "temperature reached" timer
#define TEMP_HYSTERESIS          3  // (°C) Temperature proximity considered "close enough" to the target
#define TEMP_BED_RESIDENCY_TIME 10  // (seconds) Time to wait for bed to "settle" in M190
#define TEMP_BED_WINDOW          1  // (°C) Temperature proximity for the "temperature reached" timer
#define TEMP_BED_HYSTERESIS      3  // (°C) Temperature proximity considered "close enough" to the target
#define HEATER_0_MINTEMP   5
#define HEATER_1_MINTEMP   5
#define HEATER_2_MINTEMP   5
#define HEATER_3_MINTEMP   5
#define HEATER_4_MINTEMP   5
#define HEATER_5_MINTEMP   5
#define HEATER_6_MINTEMP   5
#define HEATER_7_MINTEMP   5
#define BED_MINTEMP        5
#define HEATER_0_MAXTEMP 275
#define HEATER_1_MAXTEMP 275
#define HEATER_2_MAXTEMP 275
#define HEATER_3_MAXTEMP 275
#define HEATER_4_MAXTEMP 275
#define HEATER_5_MAXTEMP 275
#define HEATER_6_MAXTEMP 275
#define HEATER_7_MAXTEMP 275
#define BED_MAXTEMP      125
#define PIDTEMP
#define BANG_MAX 255     // Limits current to nozzle while in bang-bang mode; 255=full current
#define PID_MAX BANG_MAX // Limits current to nozzle while PID is active (see PID_FUNCTIONAL_RANGE below); 255=full current
#define PID_K1 0.95      // Smoothing factor within any PID loop
  #define PID_EDIT_MENU         // Add PID editing to the "Advanced Settings" menu. (~700 bytes of PROGMEM)
  #define PID_AUTOTUNE_MENU     // Add PID auto-tuning to the "Advanced Settings" menu. (~250 bytes of PROGMEM)
    #if PRINTER_NUMBER == 1
      #define DEFAULT_Kp 30.64
      #define DEFAULT_Ki 3.16
      #define DEFAULT_Kd 74.30
    #elif PRINTER_NUMBER == 2
      #define DEFAULT_Kp 23.52
      #define DEFAULT_Ki 1.81
      #define DEFAULT_Kd 76.37
    #elif PRINTER_NUMBER == 3
      #define DEFAULT_Kp 32.21
      #define DEFAULT_Ki 3.59
      #define DEFAULT_Kd 72.29
    #elif PRINTER_NUMBER == 4
      #define DEFAULT_Kp 32.70
      #define DEFAULT_Ki 3.71
      #define DEFAULT_Kd 72.08
    #else
      #define DEFAULT_Kp  21.73
      #define DEFAULT_Ki   1.54
      #define DEFAULT_Kd  76.55
    #endif
#define PIDTEMPBED
#define MAX_BED_POWER 255 // limits duty cycle to bed; 255=full current
  #if PRINTER_NUMBER == 1
    #define DEFAULT_bedKp 113.83
    #define DEFAULT_bedKi 21.51
    #define DEFAULT_bedKd 401.51
  #elif PRINTER_NUMBER == 2
    #define DEFAULT_bedKp 24.40
    #define DEFAULT_bedKi 4.06
    #define DEFAULT_bedKd 97.82
  #elif PRINTER_NUMBER == 3
    #define DEFAULT_bedKp 104.01
    #define DEFAULT_bedKi 20.27
    #define DEFAULT_bedKd 355.78
  #elif PRINTER_NUMBER == 4
    #define DEFAULT_bedKp 212.50
    #define DEFAULT_bedKi 35.34
    #define DEFAULT_bedKd 851.79
  #else
    #define DEFAULT_bedKp 50.71
    #define DEFAULT_bedKi 9.88
    #define DEFAULT_bedKd 173.43
  #endif
  #define PID_FUNCTIONAL_RANGE 10 // If the temperature difference between the target temperature and the actual temperature
#define PREVENT_COLD_EXTRUSION
#define EXTRUDE_MINTEMP 170
#define PREVENT_LENGTHY_EXTRUDE
#define EXTRUDE_MAXLENGTH 600
#define THERMAL_PROTECTION_HOTENDS // Enable thermal protection for all extruders
#define THERMAL_PROTECTION_BED     // Enable thermal protection for the heated bed
#define THERMAL_PROTECTION_CHAMBER // Enable thermal protection for the heated chamber
#define USE_XMIN_PLUG
#define USE_YMIN_PLUG
#define USE_ZMIN_PLUG
#define ENDSTOPPULLUPS
#define X_MIN_ENDSTOP_INVERTING false // Set to true to invert the logic of the endstop.
#define Y_MIN_ENDSTOP_INVERTING false // Set to true to invert the logic of the endstop.
#define Z_MIN_ENDSTOP_INVERTING false // Set to true to invert the logic of the endstop.
#define X_MAX_ENDSTOP_INVERTING false // Set to true to invert the logic of the endstop.
#define Y_MAX_ENDSTOP_INVERTING false // Set to true to invert the logic of the endstop.
#define Z_MAX_ENDSTOP_INVERTING false // Set to true to invert the logic of the endstop.
#define Z_MIN_PROBE_ENDSTOP_INVERTING false // Set to true to invert the logic of the probe.
#define X_DRIVER_TYPE  TMC2209
#define Y_DRIVER_TYPE  TMC2209
#define Z_DRIVER_TYPE  TMC2209
#define E0_DRIVER_TYPE TMC2209
#if PRINTER_NUMBER == 1
  #define DEFAULT_AXIS_STEPS_PER_UNIT   { 80, 80, 400, 360}  // 03/24/2021: E3D Hemera (Direct Drive 1.75mm 24V)
#elif PRINTER_NUMBER == 2
  #define DEFAULT_AXIS_STEPS_PER_UNIT   { 81, 81, 401, 360}  // 01/27/2021: E3D Hemera (Direct Drive 1.75mm 24V)
#elif PRINTER_NUMBER == 3
  #define DEFAULT_AXIS_STEPS_PER_UNIT   { 81, 81, 405, 360}  // 04/25/2021: E3D Hemera (Direct Drive 1.75mm 24V)
#elif PRINTER_NUMBER == 4
  #define DEFAULT_AXIS_STEPS_PER_UNIT   { 80, 80, 400, 360}  // 01/27/2021: E3D Hemera (Direct Drive 1.75mm 24V)
#else
  #define DEFAULT_AXIS_STEPS_PER_UNIT   { 80, 80, 400, 93 }
#endif
#define DEFAULT_MAX_FEEDRATE          { 500, 500, 5, 25 }
#if PRINTER_NUMBER == 1
  #define DEFAULT_MAX_ACCELERATION      { 500, 500, 100, 5000 }   //Hemera with V6 Hotend
#elif PRINTER_NUMBER == 2
  #define DEFAULT_MAX_ACCELERATION      { 500, 500, 100, 5000 }   //Hemera with V6 Hotend
#elif PRINTER_NUMBER == 3 || PRINTER_NUMBER == 4
  #define DEFAULT_MAX_ACCELERATION      { 1000, 1000, 1000, 5000 }   //Hemera with V6 Hotend
#else
#endif
#define DEFAULT_ACCELERATION          500    // X, Y, Z and E acceleration for printing moves
#define DEFAULT_RETRACT_ACCELERATION  500    // E acceleration for retracts
#define DEFAULT_TRAVEL_ACCELERATION   500    // X, Y, Z acceleration for travel (non printing) moves
#define DEFAULT_EJERK    5.0  // May be used by Linear Advance
  #define JUNCTION_DEVIATION_MM 0.08  // (mm) Distance from real junction edge
  #define JD_HANDLE_SMALL_SEGMENTS    // Use curvature estimation instead of just the junction angle
#define S_CURVE_ACCELERATION
#define Z_MIN_PROBE_USES_Z_MIN_ENDSTOP_PIN
#if PRINTER_NUMBER == 1 || PRINTER_NUMBER == 3 || PRINTER_NUMBER == 4
  #define USE_PROBE_FOR_Z_HOMING
#else
#endif
#if PRINTER_NUMBER == 1 || PRINTER_NUMBER == 3 || PRINTER_NUMBER == 4
  #define FIX_MOUNTED_PROBE
#else
#endif
#if PRINTER_NUMBER == 1
  #define NOZZLE_TO_PROBE_OFFSET { -39, 14, -1.0 }    // IR Probe on Hemera
#elif PRINTER_NUMBER == 3
  #define NOZZLE_TO_PROBE_OFFSET { -39, 14, -1.2 }    // IR Probe on Hemera
#elif PRINTER_NUMBER == 4
  #define NOZZLE_TO_PROBE_OFFSET { -39, 14, -0.3 }    // IR Probe on Hemera
#else
  #define NOZZLE_TO_PROBE_OFFSET { 10, 10, 0 }
#endif
#if PRINTER_NUMBER == 1 || PRINTER_NUMBER == 3 || PRINTER_NUMBER == 4
  #define PROBING_MARGIN 50
#else
  #define PROBING_MARGIN 10
#endif
#define XY_PROBE_SPEED (133*60)
#define Z_PROBE_SPEED_FAST HOMING_FEEDRATE_Z
#define Z_PROBE_SPEED_SLOW (Z_PROBE_SPEED_FAST / 2)
#if PRINTER_NUMBER == 1 || PRINTER_NUMBER == 3 || PRINTER_NUMBER == 4
  #define MULTIPLE_PROBING 2
  #define EXTRA_PROBING    1
#else
#endif
#define Z_CLEARANCE_DEPLOY_PROBE   10 // Z Clearance for Deploy/Stow
#define Z_CLEARANCE_BETWEEN_PROBES  5 // Z Clearance between probe points
#define Z_CLEARANCE_MULTI_PROBE     5 // Z Clearance between multiple probes
#define Z_PROBE_LOW_POINT          -2 // Farthest distance below the trigger-point to go before stopping
#define Z_PROBE_OFFSET_RANGE_MIN -20
#define Z_PROBE_OFFSET_RANGE_MAX 20
#define X_ENABLE_ON 0
#define Y_ENABLE_ON 0
#define Z_ENABLE_ON 0
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

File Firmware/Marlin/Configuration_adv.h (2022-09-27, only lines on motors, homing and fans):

#define E0_AUTO_FAN_PIN -1
#define E1_AUTO_FAN_PIN -1
#define E2_AUTO_FAN_PIN -1
#define E3_AUTO_FAN_PIN -1
#define E4_AUTO_FAN_PIN -1
#define E5_AUTO_FAN_PIN -1
#define E6_AUTO_FAN_PIN -1
#define E7_AUTO_FAN_PIN -1
#define CHAMBER_AUTO_FAN_PIN -1
#define HOMING_BUMP_MM      { 5, 5, 2 }       // (mm) Backoff from endstops after first bump
#define HOMING_BUMP_DIVISOR { 2, 2, 4 }       // Re-Bump Speed Divisor (Divides the Homing Feedrate)
#define QUICK_HOME                            // If G28 contains XY do a diagonal move first
#define MICROSTEP_MODES { 16, 16, 16, 16, 16, 16 } // [1,2,4,8,16]
#define ADVANCED_PAUSE_FEATURE
  #define ADVANCED_PAUSE_PURGE_FEEDRATE        3  // (mm/s) Extrude feedrate (after loading). Should be slower than load feedrate.
  #define ADVANCED_PAUSE_PURGE_LENGTH          2  // (mm) Length to extrude after loading.
  #define ADVANCED_PAUSE_RESUME_PRIME          0  // (mm) Extra distance to prime nozzle after returning from park.
    #define X_CURRENT       580        // (mA) RMS current. Multiply by 1.414 for peak current.
    #define X_CURRENT_HOME  X_CURRENT  // (mA) RMS current for sensorless homing
    #define X_MICROSTEPS     16    // 0..256
    #define Y_CURRENT       580
    #define Y_CURRENT_HOME  Y_CURRENT
    #define Y_MICROSTEPS     16
    #define Z_CURRENT       580
    #define Z_CURRENT_HOME  Z_CURRENT
    #define Z_MICROSTEPS     16
    #define E0_MICROSTEPS    16
  #define X_HYBRID_THRESHOLD     100  // [mm/s]
  #define X2_HYBRID_THRESHOLD    100
  #define Y_HYBRID_THRESHOLD     100
  #define Y2_HYBRID_THRESHOLD    100
  #define Z_HYBRID_THRESHOLD       3
  #define Z2_HYBRID_THRESHOLD      3
  #define Z3_HYBRID_THRESHOLD      3
  #define Z4_HYBRID_THRESHOLD      3
  #define E0_HYBRID_THRESHOLD     30
  #define E1_HYBRID_THRESHOLD     30
  #define E2_HYBRID_THRESHOLD     30
  #define E3_HYBRID_THRESHOLD     30
  #define E4_HYBRID_THRESHOLD     30
  #define E5_HYBRID_THRESHOLD     30
  #define E6_HYBRID_THRESHOLD     30
  #define E7_HYBRID_THRESHOLD     30

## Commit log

2020-12-15 Switched to HTML
2020-12-15 Added marlin logo
2020-12-15 Adjusted marlin logo height
2020-12-15 Cropped Marlin logo
2020-12-15 Re-uploading marlin logo
2020-12-15 Added volcano nozzles to parts list
2020-12-16 Added section about filament MVS
2020-12-16 Flashed firmware to printer 4.
    [Configuration.h, Configuration_adv.h]
2020-12-17 Flashed firmware to printer 4
    [Configuration.h, Configuration_adv.h]
2020-12-18 Added "upgrades" section
    [volcanoFanDuct.stl]
2020-12-20 Added IR probe mount
    [volcanoFanDuctWithIRProbe.stl]
2020-12-20 printer02: removed BLTouch. Added 0.4mm nozzle
    [Configuration.h]
2020-12-20 Began printing fan shroud for volcano part cooling
    [Configuration.h, cube.stl]
2020-12-21 Added upgrades
    [Raspberry_Pi_2_Case_For_Creality_Ender_3_Pro_v054.stl, body.stl, bushing.stl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]
2020-12-25 Added fan shroud to printer 02
    [Configuration.h]
2020-12-25 Changed PID tuning to include 10 cycles
2020-12-25 Fixed overwrite of printer04 with printer02 data
    [Configuration.h]
2020-12-25 Increased PID tuning to 15 cycles
2020-12-25 Ran PID tuning values
    [Configuration.h]
2020-12-25 Added shims for feeder spring tensioning
    [Shim_1mm.stl, Shim_2mm.stl]
2020-12-25 Added linear advance to printer02
    [Configuration_adv.h]
2020-12-25 PID tuned printer04
    [Configuration.h]
2020-12-29 Recalibrated PID values to adjust for colder room
    [Configuration.h]
2020-12-29 Re-dimensioned IR probe mount
    [volcanoFanDuct.stl, volcanoFanDuctWithIRProbe.stl]
2021-01-05 Added more upgrades
    [Configuration.h, IKEA-LACK-BRACKET-DRYWALL-SCREWS.stl, Raspberry_Pi_2_Case_For_Creality_Ender_3_Pro_v054.stl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]
2021-01-07 Resliced with lowered IR probe mount
    [volcanoDuctWithIRProbe.stl, volcanoFanDuctWithIRProbe.stl]
2021-01-08 Flashed firmware to printer03.
    [Configuration.h]
2021-01-08 Removed corners colliding with fan shroud
    [directDriveBracket.stl]
2021-01-08 Sliced lower v-slot covers
    [slot_cover_143mm_original.stl]
2021-01-12 Recompiled printer02 firmware for wireless flash
    [Configuration.h]
2021-01-12 Sliced v-slot covers
    [slot_cover_105mm.stl, slot_cover_175mm.stl]
2021-01-12 Lowered position of probe
    [legExtension.stl, volcanoDuctWithIRProbe.stl, volcanoFanDuct.stl]
2021-01-12 printer02: configured z-probe
    [Configuration.h]
2021-01-12 printer02: configured UBL
    [Configuration.h]
2021-01-12 printer02: enabled RESTORE_LEVELING_AFTER_G28
    [Configuration.h]
2021-01-12 printer02: Removed UBL and LCD leveling. Added 3pt
    [Configuration.h]
2021-01-12 printer02: switched to bilinear ABL
    [Configuration.h]
2021-01-12 printer02: switched probe from PT-DET to SERVO
    [Configuration.h]
2021-01-12 printer02: Using PT-DET pin for IR probe
    [Configuration.h]
2021-01-12 printer02: switched to PC12 for probe
2021-01-12 printer02: reverted to default IR probe pins
    [Configuration.h]
2021-01-16 Added holes for screwing shower curtain into
    [legExtension.stl]
2021-01-22 Recompiled firmware for Hemera on printer02
    [Configuration.h, Ender3-Hemera_V4.stl, Prusa_Enclosure_Spool_Holder.stl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]
2021-01-23 Reslicing for acceleration tuning
    [Single_Layer_Disc.stl]
2021-01-23 Rebuilt without linear advance
    [Configuration.h, Configuration_adv.h]
2021-01-27 Began working on cable chain
    [3CableLinks.stl]
2021-01-27 Mounting hemera to printer04
2021-03-24 Pre-Flashing new firmware
    [Configuration.h, Configuration_adv.h]
2021-03-24 Added z_after_homing to printer01
    [Configuration.h]
2021-03-24 Reconfigured printer01 slave addresses
    [Configuration.h, Configuration_adv.h]
2021-03-24 Added error documentation in bed PID tuning
2021-03-24 Added bed PID values
    [Configuration.h]
2021-03-24 Enabled controller (motherboard/stepper) fan
    [Configuration_adv.h]
2021-04-19 printer01: Added ABL
    [Configuration.h, Configuration_adv.h, probe_mount.stl]
2021-04-19 printer01: Enabled fwretract of 0.5mm
    [Configuration_adv.h]
2022-09-27 Added printer specific config, part removes, RPi4 case.
    [Configuration.h, Configuration_adv.h]

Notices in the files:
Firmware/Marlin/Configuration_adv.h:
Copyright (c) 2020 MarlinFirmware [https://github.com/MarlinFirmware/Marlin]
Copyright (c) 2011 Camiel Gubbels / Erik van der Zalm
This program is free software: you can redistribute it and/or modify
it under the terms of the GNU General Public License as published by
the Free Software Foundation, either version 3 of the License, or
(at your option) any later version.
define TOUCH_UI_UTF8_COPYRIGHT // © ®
